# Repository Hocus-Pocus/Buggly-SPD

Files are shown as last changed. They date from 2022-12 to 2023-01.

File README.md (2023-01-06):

# Buggly-SPD
Programmable engine management for the air cooled VW Dual Port 1600 with Mexican EFI OEM parts. The board is a stripped down, "no frills" variant of the official Speeduino V4.4 board with one particular application in mind. A stock, or relatively stock, air cooled VW dual port 1600 engine being converted to EFI using most of the OEM hardware from the Mexican 1600i, and a 36-1 trigger wheel with a VR CKP sensor. It is designed to use waste spark ignition and injectors paired 1&3, 2&4, fired 2 times alternating over the 720 degree engine cycle. The injector pulse is scheduled to be finished when the intake valve reaches the end of its effective duration. With a firing order of 1-4-3-2, half the fuel is injected on an open intake valve, and the other half is injected on a closed intake valve. This should result in a smoother running engine at all speeds and loads as each cylinder gets the same balanced charge mix. This board connects to the Arduino Mega 2560 and is housed in a Hammond enclosure. It has a power supply for the Mega and does all the low voltage processing. It connects to the Buggly Aux board, also in a Hammond enclosuer that has the high current outputs, fuses, relays and terminal strips for connection to vehicle wiring. Header for a Blutooth module added 1-06-23.

  WORK IN PROGRESS

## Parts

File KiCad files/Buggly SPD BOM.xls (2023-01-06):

Buggly SPD BOM
Assignment | Qty | Description | Mfgr | Mfgr # | Digikey #
C17,19,21 | 3 | 10,000pf | Kemet | C315C103K5R5TA | 399-4148-ND
C7,8 | 2 | 47pf | Kemet | C315C470J5G5TA | 399-9737-ND
C5,6,13,14,15,16 | 6 | 0.22uf | Kemet | C320C224K5R5TA | 399-4288-ND
C26 | 1 | 47uf | Panasonic | EEU-FC1H470B | P19658CT-ND
C18,20 | 2 | 1uf | TDK | FK14X7R1E105K | 445-5315-ND
C22 | 1 | 22uf | TDK | FA22X7R1E226MRU06 | 445-180603-1-ND
C1,2,3,4,9,10,11,12,24,25 | 10 | 0.1uf | TDK | FA18X8R1E104KNU06 | 445-180563-1-ND
C23 | 1 | 10uf | Panasonic | EEU-FC1H100LB | P19649CT-ND
D17 | 1 | Diode | Micro | 1N5818-TP | iN5818-TPCT-ND
IC1 | 1 | TVS Array | Little Fuse | SP721APP | F2720-ND
Arduino pins (36) | 1 | Header pins | Amp | 75160-105-36LF | 609-6393-ND
F1 | 1 | Reset Fuse | Bourns | MF-R050 | MF-R050-ND
J15 | 1 | DB25 | Wurth | 618025231221 | 732-618025231221-ND
U1 | 1 | MAP Sensor | NXP | MPXH6115AC6U | MPXH6115AC6U-ND
U1 header pins | 1 | 90 degree | Molex | 0022122041 | 23-0022122041-ND
U3,4,5,6 | 4 | Gate Driver | IXYS | IXDN604PI | CLA335-ND
Sockets for VR Cond, U1,2 | 4 | 4 pos Pin Sockets | 3M | 929850-01-04-10 | 929850-01-04-10
U6 | 1 | Solenoid Driver | STM | ULN2001A | 497-2340-5-ND
U6 socket | 1 | 16 DIP | MillMax | 110-13-316-41-001000 | ED56163-ND
IC1,J16,U3,4,5,6 sockets | 6 | 8 DIP | CNC Tech | 210-1-08-003 | 1175-1467-ND
U7 | 1 | 5V reg | Texas Inst | LM2940T-5.0 | LM2940T-5.0-ND
R3,4,9,10,11,12 | 10 | 470R | Yageo | CFR-25-JB-52-470R | 470QBK-ND
R18 | 1 | 4.7K | Yageo | CFR-25-JB-52-4K7 | 4.7KQBK-ND
R17 | 1 | 24K | Yageo | CFR-25-JB-52-24K | 24KQBK-ND
R19,27,30,31,32,33,34 | 7 | 1K | Yageo | CFR-25-JB-52-1K | 1.0KQBK-ND
R7,8 | 2 | 2.49K | Yageo | 25-FBF-52-2K29 | 2.49KXBK-ND
R13,14,15,35 | 4 | 22R | Stackpole | CF14JT22R0 | CF14JT22R0CT-ND
R16,24,25,26,28,29 | 6 | 100R | Yageo | CFR-25-JB-52-100R | 100QBK-ND
R1 | 1 | 1K 1% | Stackpole | RNMF14FTD1K00 | RNF14FTD1K00CT-ND
R2 | 1 | 3.9K 1% | Stackpole | RNMF14TCK390 | S3.9KCACT-ND
R5,6 | 2 | 51K | Stackpole | CF14JT51K0 | CF14JT51KOCT-ND
RV1 | 1 | Varistor | Panasonic | ERZ-V14D220 | P7307-ND
Q1 | 1 | PNP transistor | Micro | 2N3906-AP | 2N39006-APCT-ND

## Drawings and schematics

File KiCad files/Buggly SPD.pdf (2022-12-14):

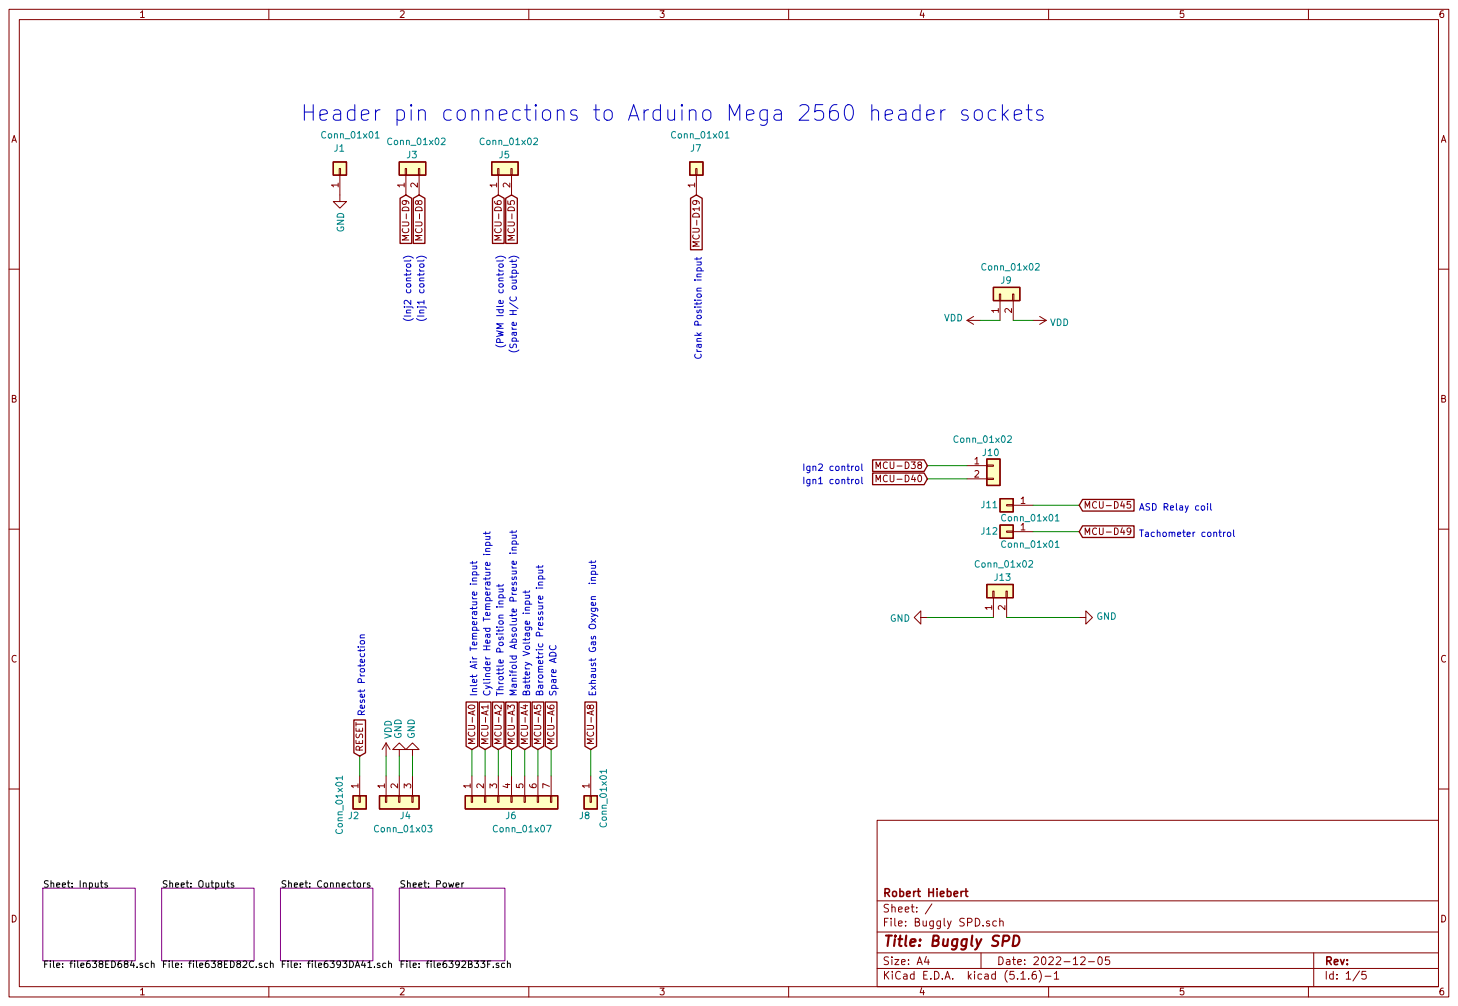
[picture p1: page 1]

Header pin connections to Arduino Mega 2560 header sockets Crank Position input

Ign2 control Spare ADC (Spare H/C output)

ASD Relay coil Tachometer control Reset Protection

Id: 1/5 Title: Buggly SPD

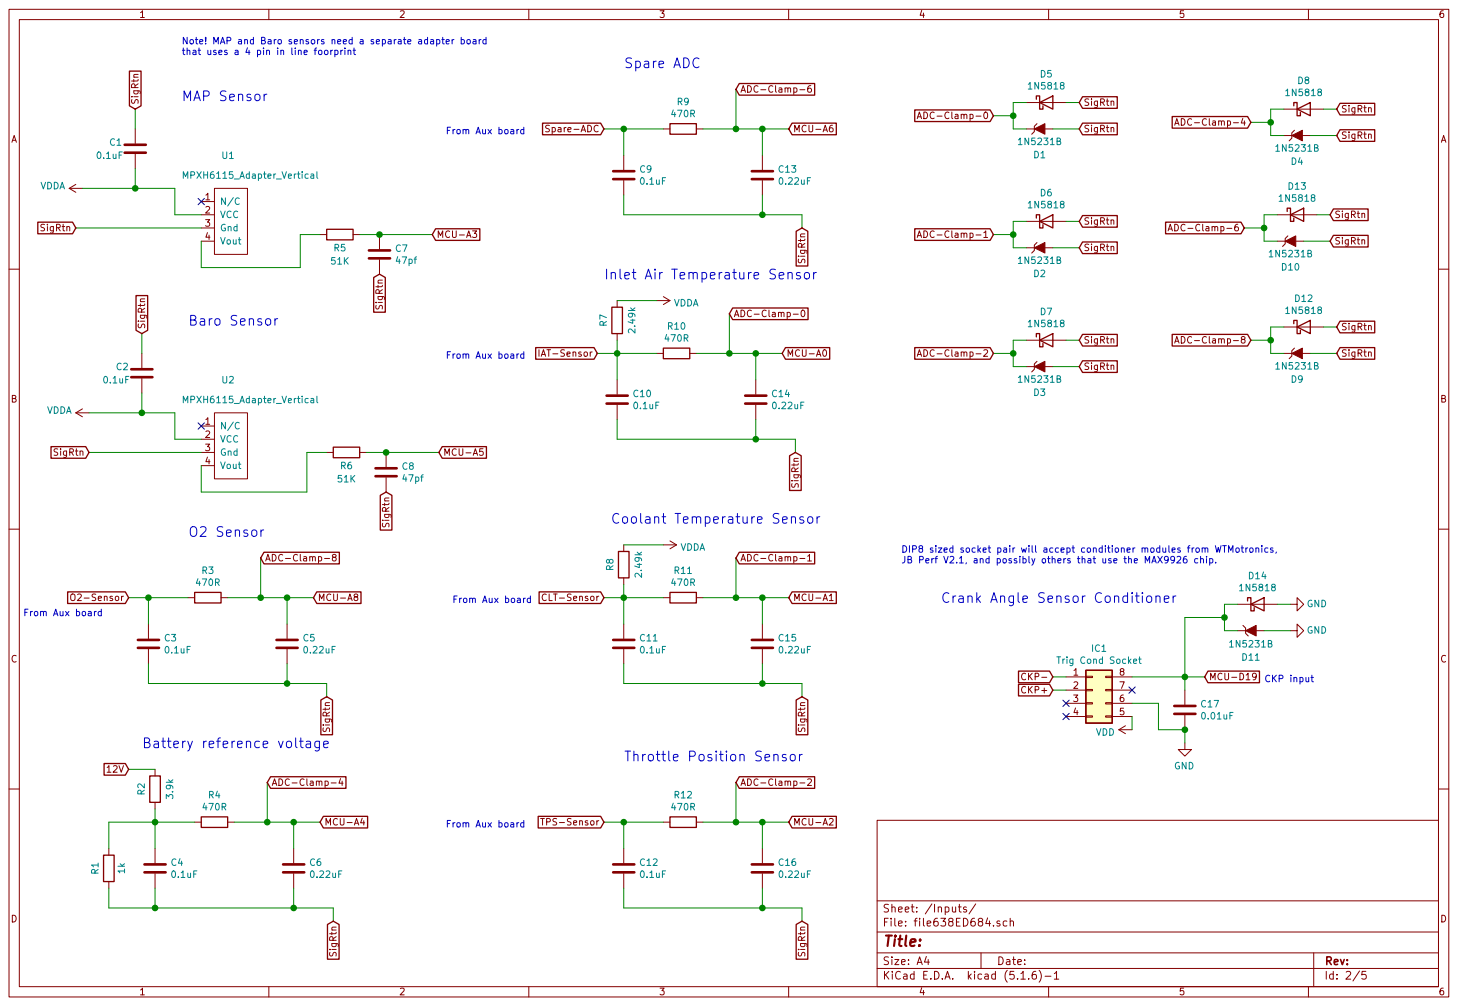
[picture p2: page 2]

Note! MAP and Baro sensors need a separate adapter board
that uses a 4 pin in line foorprint

From Aux board MAP Sensor

IAT-Sensor MCU-A5 MCU-A3 SigRtn

DIP8 sized socket pair will accept conditioner modules from WTMotronics,
JB Perf V2.1, and possibly others that use the MAX9926 chip.

Crank Angle Sensor Conditioner

Id: 2/5 Title: File: file638ED684.sch Sheet: /Inputs/

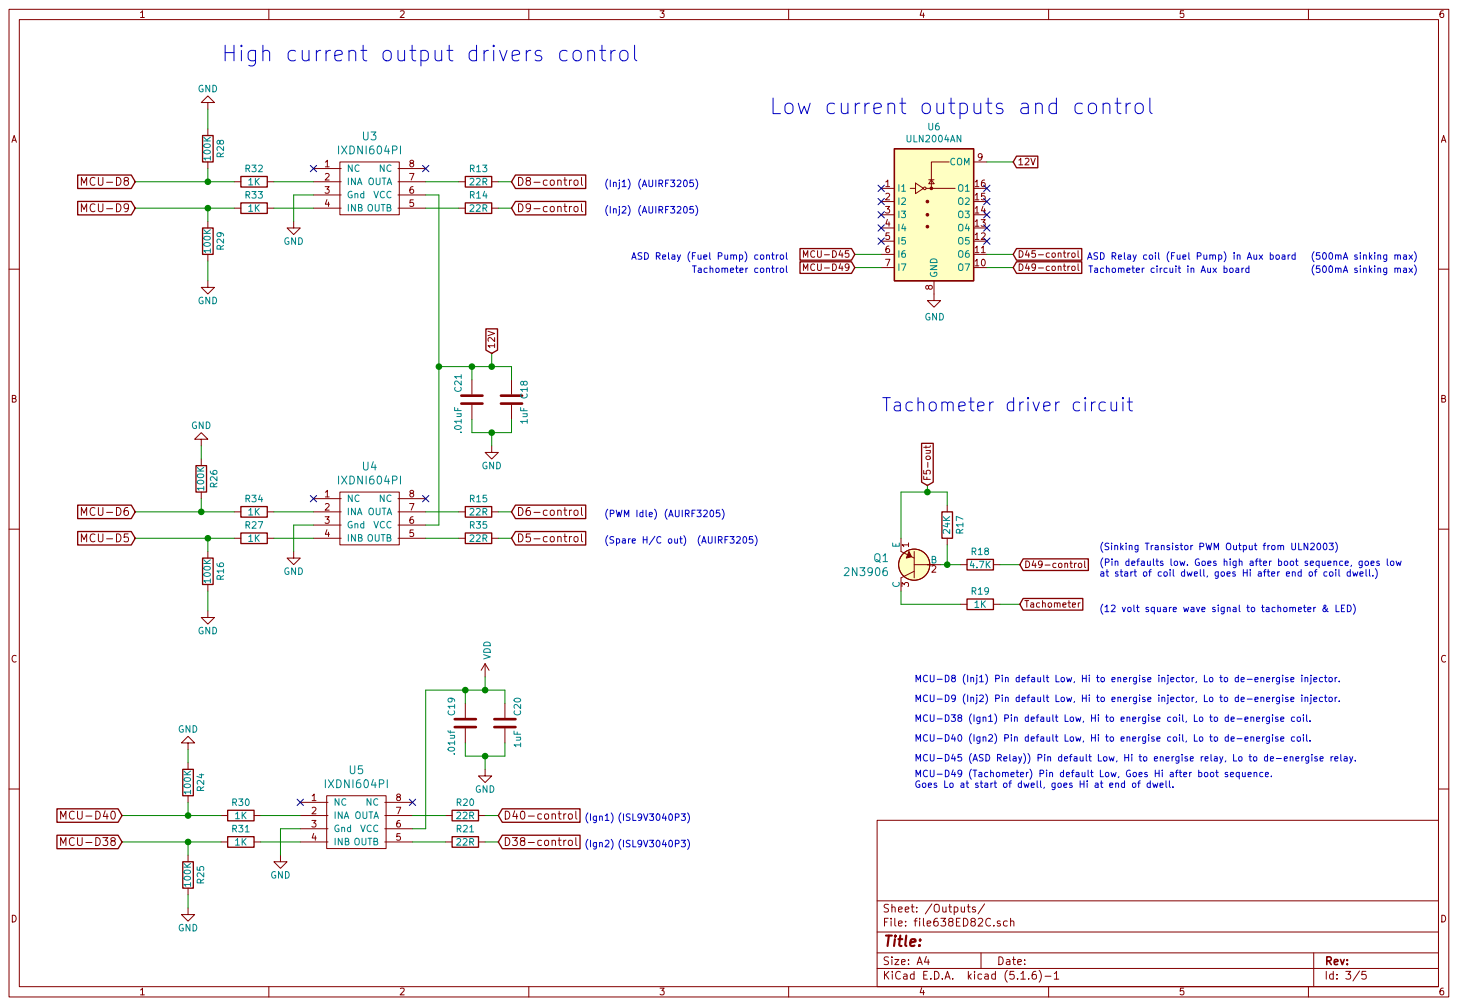
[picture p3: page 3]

Low current outputs and control

8 COM 9 U6 ULN2004AN GND 100K R25 C18 1uF GND GNDGND GND GND

ASD Relay coil (Fuel Pump) in Aux board

(Sinking Transistor PWM Output from ULN2003)
(Pin defaults low. Goes high after boot sequence, goes low
at start of coil dwell, goes Hi after end of coil dwell.)

(12 volt square wave signal to tachometer & LED)

MCU-D8 (Inj1) Pin default Low, Hi to energise injector, Lo to de-energise injector.
MCU-D9 (Inj2) Pin default Low, Hi to energise injector, Lo to de-energise injector.
MCU-D38 (Ign1) Pin default Low, Hi to energise coil, Lo to de-energise coil.
MCU-D40 (Ign2) Pin default Low, Hi to energise coil, Lo to de-energise coil.
MCU-D45 (ASD Relay)) Pin default Low, Hi to energise relay, Lo to de-energise relay.
MCU-D49 (Tachometer) Pin default Low, Goes Hi after boot sequence.
Goes Lo at start of dwell, goes Hi at end of dwell.

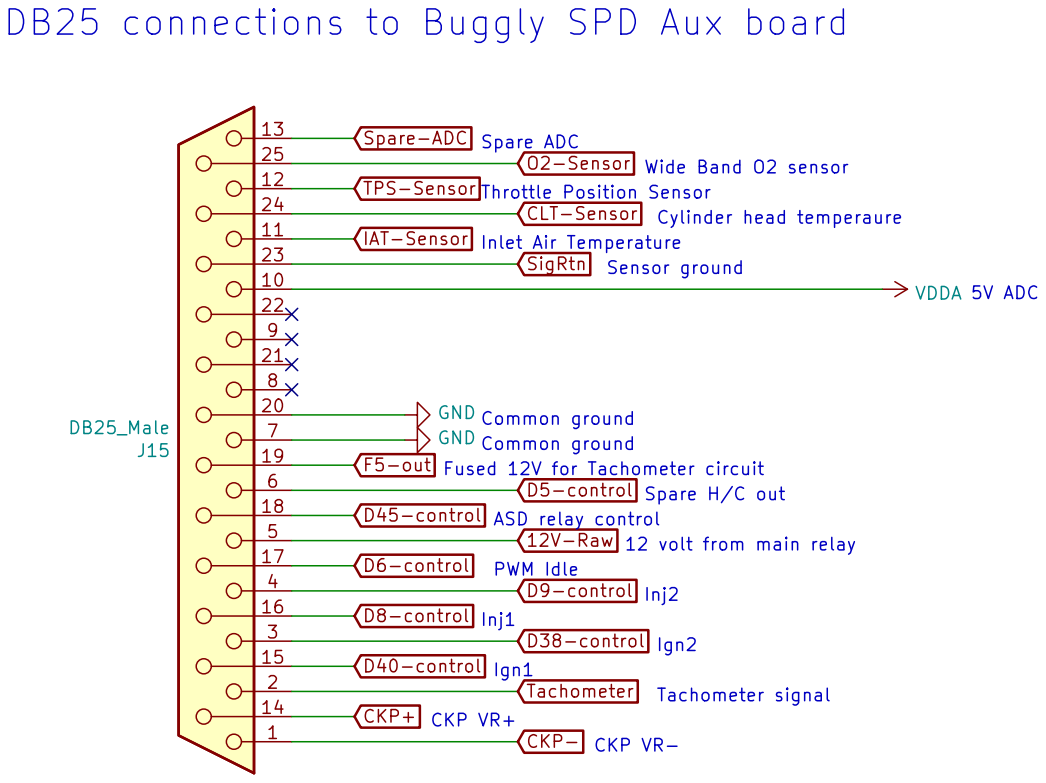
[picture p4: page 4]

5V ADC DB25 connections to Buggly SPD Aux board

Spare H/C out Fused 12V for Tachometer circuit CKP VR+ Spare ADC
Cylinder head temperaure Wide Band O2 sensor Throttle Position Sensor Sensor ground

Id: 4/5 Title: File: file6393DA41.sch Sheet: /Connectors/ GND
Common groundCKP VR-
Common ground

ASD relay control PWM Idle
12V-Raw

12 volt from main relay

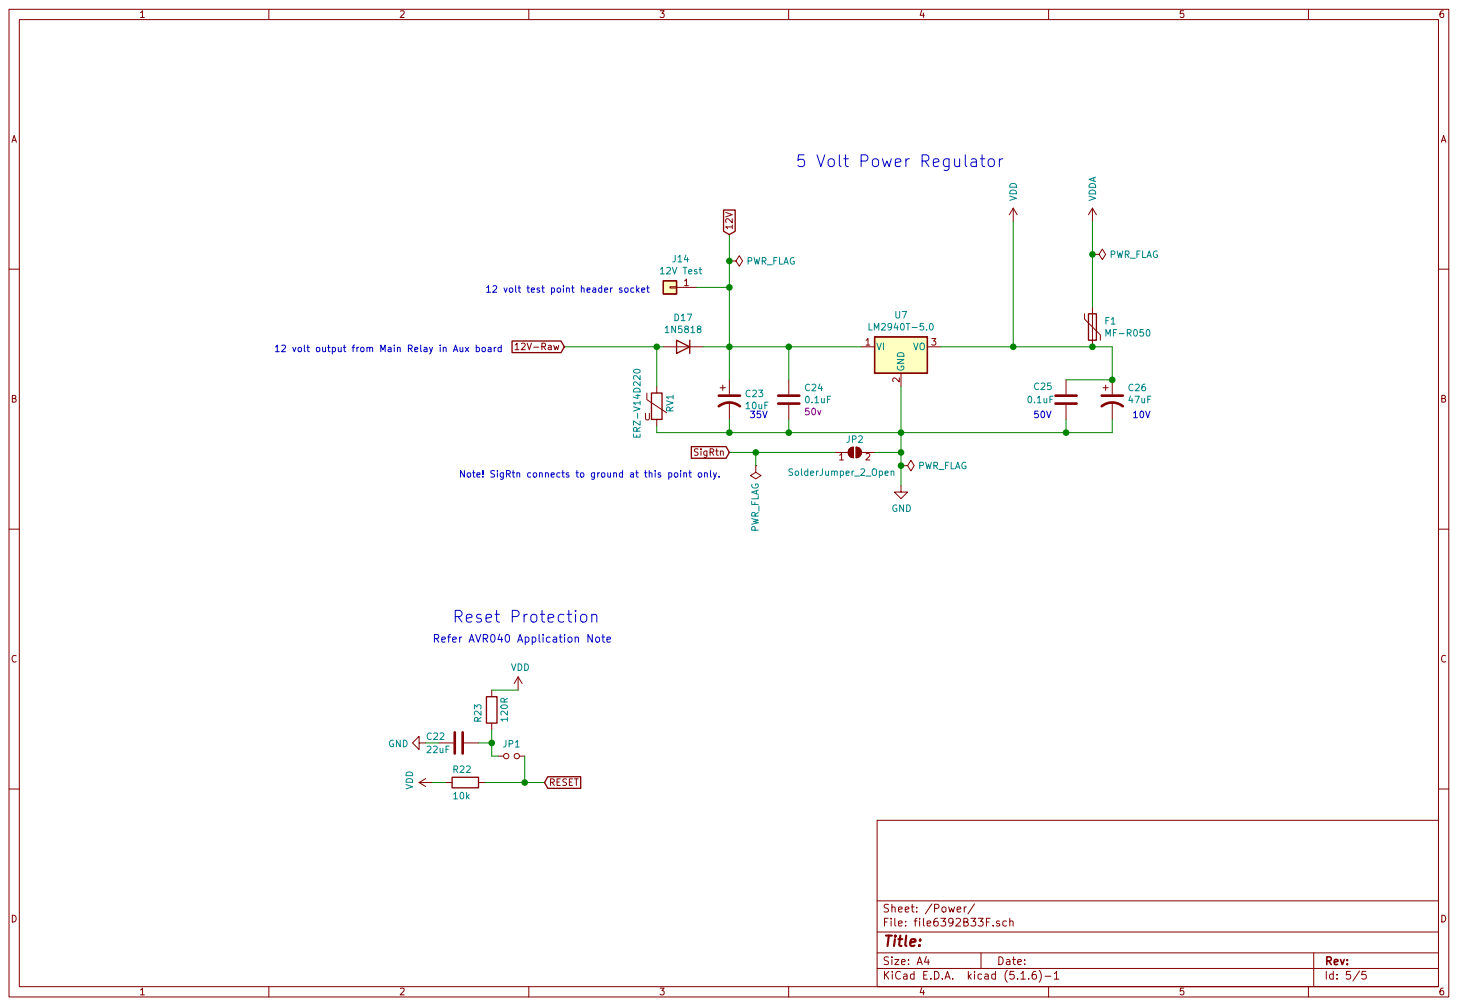
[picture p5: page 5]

12 volt test point header socket

12 volt output from Main Relay in Aux board

Note! SigRtn connects to ground at this point only.

Id: 5/5 Title: File: file6392B33F.sch Sheet: /Power/

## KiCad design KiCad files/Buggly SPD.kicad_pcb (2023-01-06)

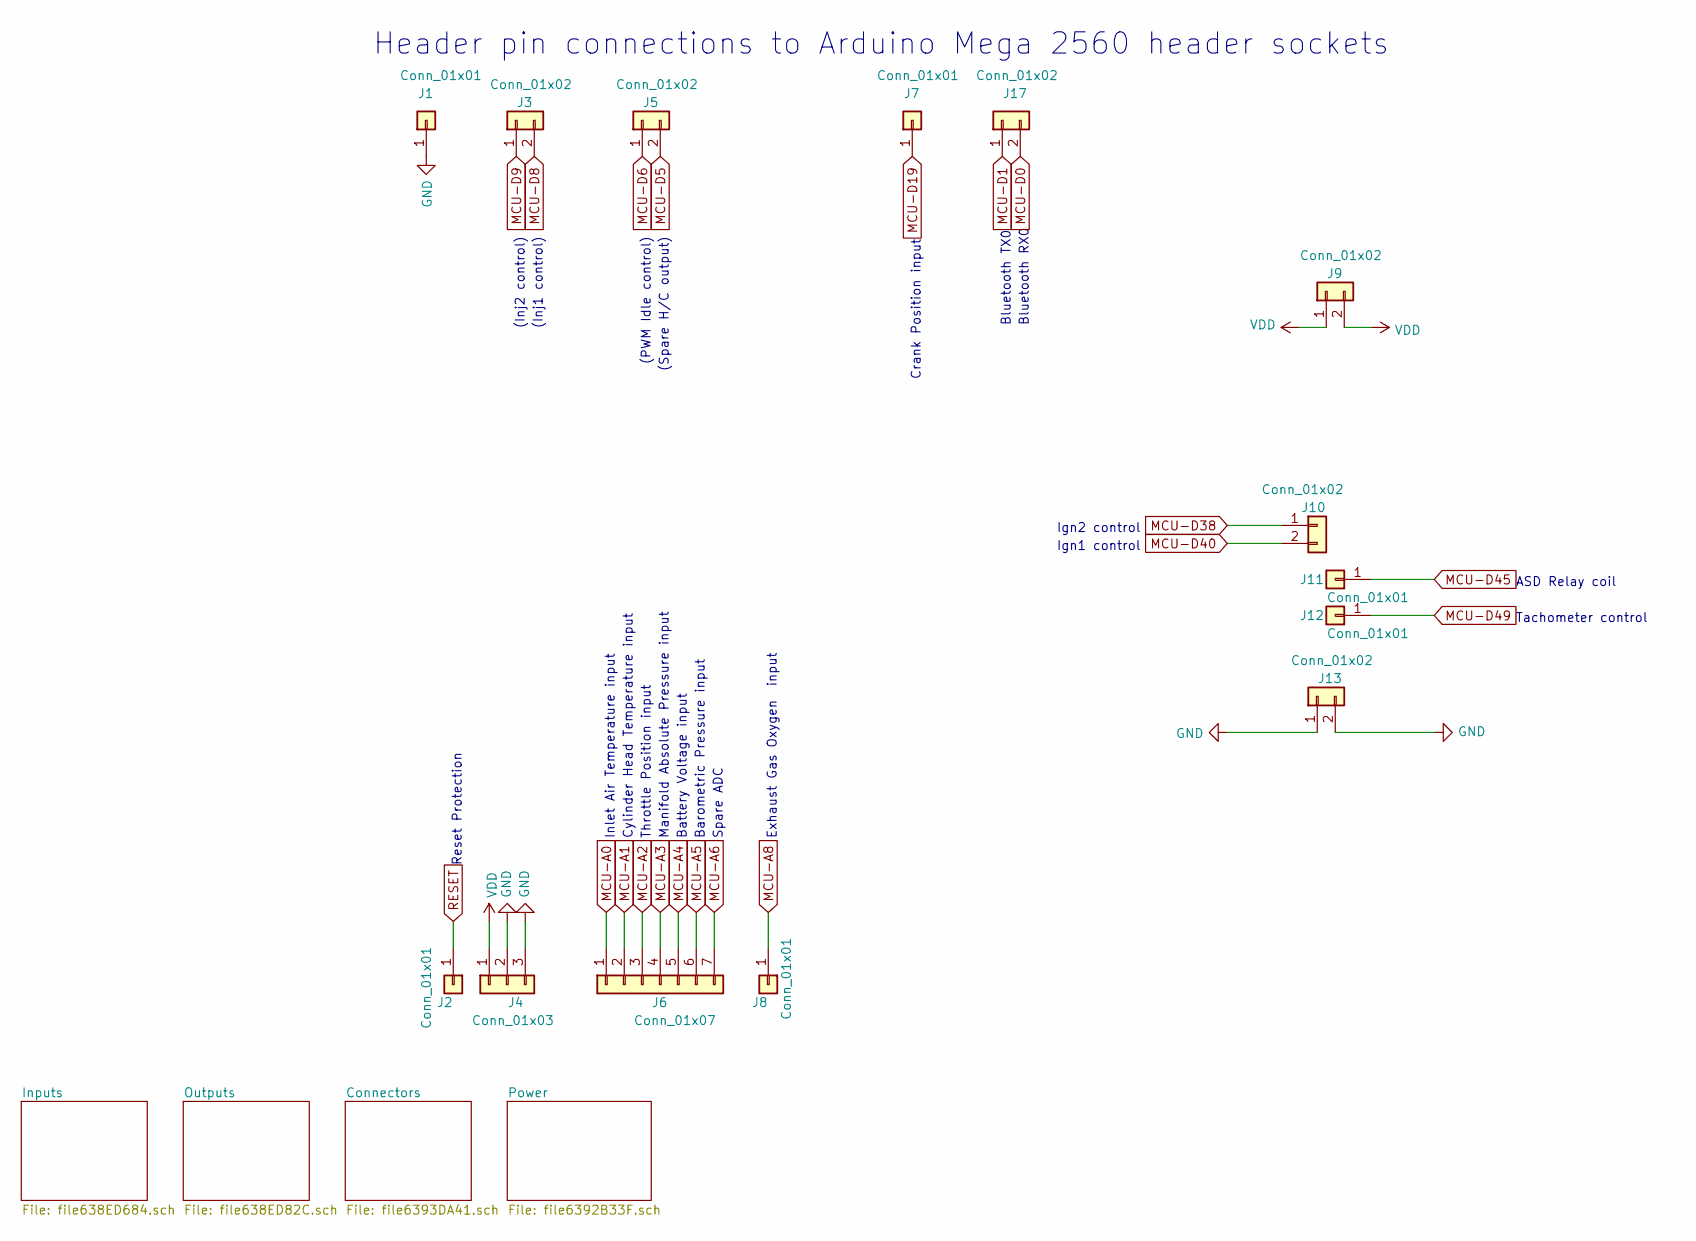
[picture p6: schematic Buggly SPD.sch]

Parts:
J1, J2, J7, J8, J11, J12: Conn_01x01; PinHeader_1x01_P2.54mm_Vertical
J3, J5, J9, J10, J13, J17: Conn_01x02; PinHeader_1x02_P2.54mm_Vertical
J4: Conn_01x03; PinHeader_1x03_P2.54mm_Vertical
J6: Conn_01x07; PinHeader_1x07_P2.54mm_Vertical

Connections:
ADC-Clamp-0: J6.1; also elsewhere on the board
ADC-Clamp-1: J6.2; also elsewhere on the board
ADC-Clamp-2: J6.3; also elsewhere on the board
ADC-Clamp-4: J6.5; also elsewhere on the board
ADC-Clamp-6: J6.7; also elsewhere on the board
ADC-Clamp-8: J8.1; also elsewhere on the board
GND: J1.1, J4.2, J4.3, J13.1, J13.2; also elsewhere on the board
MCU-A3: J6.4; also elsewhere on the board
MCU-A5: J6.6; also elsewhere on the board
MCU-D0: J17.2; also elsewhere on the board
MCU-D1: J17.1; also elsewhere on the board
MCU-D5: J5.2; also elsewhere on the board
MCU-D6: J5.1; also elsewhere on the board
MCU-D8: J3.2; also elsewhere on the board
MCU-D9: J3.1; also elsewhere on the board
MCU-D19: J7.1; also elsewhere on the board
MCU-D38: J10.1; also elsewhere on the board
MCU-D40: J10.2; also elsewhere on the board
MCU-D45: J11.1; also elsewhere on the board
MCU-D49: J12.1; also elsewhere on the board
RESET: J2.1; also elsewhere on the board
VDD: J4.1, J9.1, J9.2; also elsewhere on the board

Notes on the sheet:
Ign1 control
ASD Relay coil
Ign2 control
Tachometer control
Reset Protection
Inlet Air Temperature input
Cylinder Head Temperature input
Throttle Position input
Exhaust Gas Oxygen input
Battery Voltage input
Manifold Absolute Pressure input
Barometric Pressure input
(Inj1 control)
(PWM Idle control)
(Inj2 control)
Header pin connections to Arduino Mega 2560 header sockets
Crank Position input
(Spare H/C output)
Spare ADC
Bluetooth RX0
Bluetooth TX0

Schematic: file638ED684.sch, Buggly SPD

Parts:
C1, C2: 0.1uF; C_Disc_D5.0mm_W2.5mm_P2.50mm; Manufacturer_Part_Number FA18X7R1H103KNU06; Digikey Part Number 445-174244-1-ND
C3, C4, C9, C10, C11, C12: 0.1uF; C_Disc_D5.0mm_W2.5mm_P2.50mm; Manufacturer_Part_Number FA18X8R1E104KNU06; Digikey Part Number 445-180563-1-ND
C5, C6, C13, C14, C15, C16: 0.22uF; C_Disc_D5.0mm_W2.5mm_P2.50mm; Manufacturer_Part_Number FA18X8R1E224KRU06; Digikey Part Number 445-180564-1-ND
C7, C8: 47pf; C_Disc_D5.0mm_W2.5mm_P2.50mm; Manufacturer_Part_Number FA18NP01H471JNU06; Digikey Part Number 445-180522-1-ND
C17: 0.01uF; C_Disc_D5.0mm_W2.5mm_P2.50mm; Manufacturer_Part_Number FA18X7R1H103KNU06; Digikey Part Number 445-174244-1-ND
IC1: Trig Cond Socket; DIP-8_W7.62mm_Socket
J16: SP721APP; DIP-8_W7.62mm
J18: Conn_01x04; PinSocket_1x04_P2.54mm_Horizontal
R1: 1k; R_Axial_DIN0207_L6.3mm_D2.5mm_P7.62mm_Horizontal; Manufacturer_Part_Number MBA02040C1001FRP00; Digikey Part Number BC1.00KXCT-ND
R2: 3.9k; R_Axial_DIN0207_L6.3mm_D2.5mm_P7.62mm_Horizontal; Manufacturer_Part_Number MBA02040C3901FCT00; Digikey Part Number BC3272CT-ND
R3, R4, R9, R10, R11, R12: 470R; R_Axial_DIN0207_L6.3mm_D2.5mm_P7.62mm_Horizontal; Manufacturer_Part_Number MBA02040C4700FRP00; Digikey Part Number BC3516CT-ND
R5, R6: 51K; R_Axial_DIN0207_L6.3mm_D2.5mm_P7.62mm_Horizontal; Manufacturer_Part_Number MBA02040C4700FRP00; Digikey Part Number BC3516CT-ND
R7, R8: 2.49k; R_Axial_DIN0207_L6.3mm_D2.5mm_P7.62mm_Horizontal; Manufacturer_Part_Number MBA02040C2491FRP00; Digikey Part Number BC2.49KXCT-ND
R36: 1K; R_Axial_DIN0207_L6.3mm_D2.5mm_P7.62mm_Horizontal; Manufacturer_Part_Number MBA02040C4700FRP00; Digikey Part Number BC3516CT-ND
R37: 2.2K; R_Axial_DIN0207_L6.3mm_D2.5mm_P7.62mm_Horizontal; Manufacturer_Part_Number MBA02040C4700FRP00; Digikey Part Number BC3516CT-ND
U1, U2: MPXH6115_Adapter_Vertical

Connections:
12V: R2.2; also elsewhere on the board
ADC-Clamp-0: C14.1, J16.1, R10.1; also elsewhere on the board
ADC-Clamp-1: C15.1, J16.2, R11.1; also elsewhere on the board
ADC-Clamp-2: C16.1, J16.3, R12.1; also elsewhere on the board
ADC-Clamp-4: C6.1, J16.5, R4.1; also elsewhere on the board
ADC-Clamp-6: C13.1, J16.6, R9.1; also elsewhere on the board
ADC-Clamp-8: C5.1, J16.7, R3.1; also elsewhere on the board
CKP+: IC1.2; also elsewhere on the board
CKP-: IC1.1; also elsewhere on the board
CLT-Sensor: C11.1, R8.1, R11.2; also elsewhere on the board
GND: C17.2, IC1.6, J18.2, R37.1; also elsewhere on the board
IAT-Sensor: C10.1, R7.1, R10.2; also elsewhere on the board
MCU-A3: C7.1, R5.1; also elsewhere on the board
MCU-A5: C8.1, R6.1; also elsewhere on the board
MCU-D0: J18.3; also elsewhere on the board
MCU-D1: R36.2; also elsewhere on the board
MCU-D19: C17.1, IC1.8; also elsewhere on the board
unnamed: C4.1, R1.2, R2.1, R4.2
unnamed: J18.4, R36.1, R37.2
unnamed: R5.2, U1.4
unnamed: R6.2, U2.4
O2-Sensor: C3.1, R3.2; also elsewhere on the board
SigRtn: C1.1, C2.1, C3.2, C4.2, C5.2, C6.2, C7.2, C8.2, C9.2, C10.2, C11.2, C12.2, C13.2, C14.2, C15.2, C16.2, J16.4, R1.1, U1.3, U2.3; also elsewhere on the board
Spare-ADC: C9.1, R9.2; also elsewhere on the board
TPS-Sensor: C12.1, R12.2; also elsewhere on the board
VDD: IC1.5, J18.1; also elsewhere on the board
VDDA: C1.2, C2.2, J16.8, R7.2, R8.2, U1.2, U2.2; also elsewhere on the board

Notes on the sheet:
MAP Sensor
O2 Sensor
Throttle Position Sensor
Inlet Air Temperature Sensor
Coolant Temperature Sensor
Battery reference voltage
Baro Sensor
From Aux board
Note! MAP and Baro sensors need a separate adapter board that uses a 4 pin in line foorprint
CKP input
DIP8 sized socket pair will accept conditioner modules from WTMotronics, JB Perf V2.1, and possibly others that use the MAX9926 chip.
Crank Angle Sensor Conditioner
Spare ADC
IAT
CLT
TPS
BAT
Spare
ADC Clamps
DSD Tech HC-06 Bluetooth module header
Gnd
BT TX
BT RX
RX0
TX0

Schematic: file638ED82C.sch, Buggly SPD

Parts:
C18, C20: 1uF; C_Disc_D5.0mm_W2.5mm_P2.50mm
C19: .01uf; C_Disc_D5.0mm_W2.5mm_P2.50mm
C21: .01uF; C_Disc_D5.0mm_W2.5mm_P2.50mm
Q1: 2N3906; TO-92_Inline_Wide; MPN 2N3906; Digi-Key_PN 2N3906CS-ND
R13, R14, R15, R20, R21, R35: 22R; R_Axial_DIN0207_L6.3mm_D2.5mm_P7.62mm_Horizontal
R16, R24, R25, R26, R28, R29: 100K; R_Axial_DIN0207_L6.3mm_D2.5mm_P7.62mm_Horizontal
R17: 24K; R_Axial_DIN0207_L6.3mm_D2.5mm_P7.62mm_Horizontal
R18: 4.7K; R_Axial_DIN0207_L6.3mm_D2.5mm_P7.62mm_Horizontal
R19, R27, R30, R31, R32, R33, R34: 1K; R_Axial_DIN0207_L6.3mm_D2.5mm_P7.62mm_Horizontal
U3, U4, U5: IXDNI604PI; DIP-8_W7.62mm
U6: ULN2004AN; DIP-16_W7.62mm; Manufacturer_Part_Number ULN2003AIN‎; Digikey Part Number 296-16971-5-ND

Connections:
12V: C18.2, C21.2, U3.6, U4.6, U6.9 (COM); also elsewhere on the board
D5-control: R35.1; also elsewhere on the board
D6-control: R15.1; also elsewhere on the board
D8-control: R13.1; also elsewhere on the board
D9-control: R14.1; also elsewhere on the board
D38-control: R21.1; also elsewhere on the board
D40-control: R20.1; also elsewhere on the board
D45-control: U6.11 (O6); also elsewhere on the board
D49-control: R18.1, U6.10 (O7)
F5-out: Q1.1 (E), R17.2; also elsewhere on the board
GND: C18.1, C19.1, C20.1, C21.1, R16.1, R24.2, R25.1, R26.2, R28.2, R29.1, U3.3, U4.3, U5.3, U6.8 (GND); also elsewhere on the board
MCU-D5: R16.2, R27.2; also elsewhere on the board
MCU-D6: R26.1, R34.2; also elsewhere on the board
MCU-D8: R28.1, R32.2; also elsewhere on the board
MCU-D9: R29.2, R33.2; also elsewhere on the board
MCU-D38: R25.2, R31.2; also elsewhere on the board
MCU-D40: R24.1, R30.2; also elsewhere on the board
MCU-D45: U6.6 (I6); also elsewhere on the board
MCU-D49: U6.7 (I7); also elsewhere on the board
unnamed: Q1.2 (B), R17.1, R18.2
unnamed: Q1.3 (C), R19.2
unnamed: R13.2, U3.7
unnamed: R14.2, U3.5
unnamed: R15.2, U4.7
unnamed: R20.2, U5.7
unnamed: R21.2, U5.5
unnamed: R27.1, U4.4
unnamed: R30.1, U5.2
unnamed: R31.1, U5.4
unnamed: R32.1, U3.2
unnamed: R33.1, U3.4
unnamed: R34.1, U4.2
unnamed: R35.2, U4.5
Tachometer: R19.1; also elsewhere on the board
VDD: C19.2, C20.2, U5.6; also elsewhere on the board

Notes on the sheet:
(Inj1)
(Inj2)
(PWM Idle)
ASD Relay coil (Fuel Pump) in Aux board
Tachometer circuit in Aux board
Tachometer control
ASD Relay (Fuel Pump) control
(Ign2)
(Ign1)
(500mA sinking max)
High current output drivers control
Low current outputs and control
MCU-D8 (Inj1) Pin default Low, Hi to energise injector, Lo to de-energise injector.
MCU-D9 (Inj2) Pin default Low, Hi to energise injector, Lo to de-energise injector.
MCU-D38 (Ign1) Pin default Low, Hi to energise coil, Lo to de-energise coil.
MCU-D40 (Ign2) Pin default Low, Hi to energise coil, Lo to de-energise coil.
MCU-D45 (ASD Relay)) Pin default Low, Hi to energise relay, Lo to de-energise relay.
MCU-D49 (Tachometer) Pin default Low, Goes Hi after boot sequence. Goes Lo at start of dwell, goes Hi at end of dwell.
(Sinking Transistor PWM Output from ULN2003)
(12 volt square wave signal to tachometer & LED)
Tachometer driver circuit
(Pin defaults low. Goes high after boot sequence, goes low at start of coil dwell, goes Hi after end of coil dwell.)
(AUIRF3205)
(ISL9V3040P3)
(Spare H/C out)

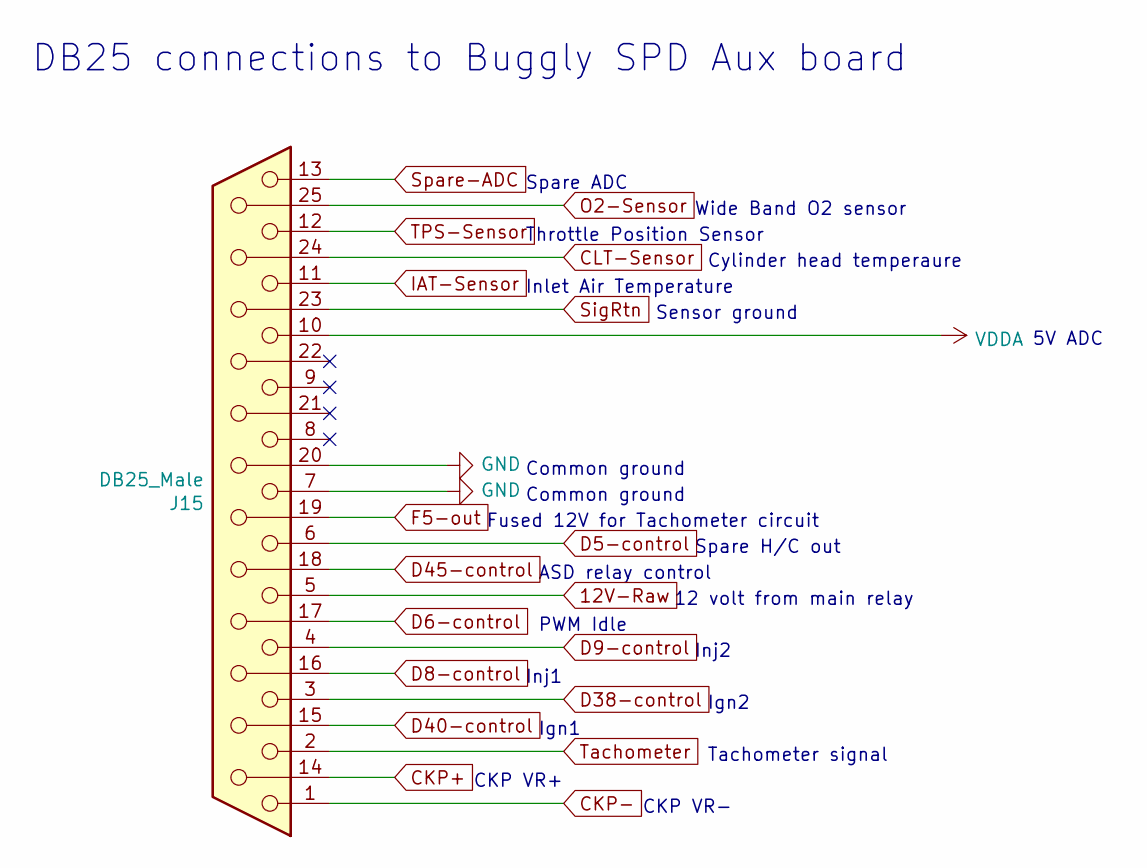
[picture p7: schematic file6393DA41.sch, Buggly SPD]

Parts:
J15: DB25_Male; DSUB-25_Male_Horizontal_P2.77x2.84mm_EdgePinOffset4.94mm_Ho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

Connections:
12V-Raw: J15.5; also elsewhere on the board
CKP+: J15.14; also elsewhere on the board
CKP-: J15.1; also elsewhere on the board
CLT-Sensor: J15.24; also elsewhere on the board
D5-control: J15.6; also elsewhere on the board
D6-control: J15.17; also elsewhere on the board
D8-control: J15.16; also elsewhere on the board
D9-control: J15.4; also elsewhere on the board
D38-control: J15.3; also elsewhere on the board
D40-control: J15.15; also elsewhere on the board
D45-control: J15.18; also elsewhere on the board
F5-out: J15.19; also elsewhere on the board
GND: J15.7, J15.20; also elsewhere on the board
IAT-Sensor: J15.11; also elsewhere on the board
O2-Sensor: J15.25; also elsewhere on the board
SigRtn: J15.23; also elsewhere on the board
Spare-ADC: J15.13; also elsewhere on the board
TPS-Sensor: J15.12; also elsewhere on the board
Tachometer: J15.2; also elsewhere on the board
VDDA: J15.10; also elsewhere on the board

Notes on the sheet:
Fused 12V for Tachometer circuit
CKP VR+
5V ADC
Inlet Air Temperature
Cylinder head temperaure
Wide Band O2 sensor
Throttle Position Sensor
Sensor ground
Common ground
CKP VR-
Ign1
ASD relay control
PWM Idle
Inj1
12 volt from main relay
DB25 connections to Buggly SPD Aux board
Spare ADC
Inj2
Tachometer signal
Ign2
Spare H/C out

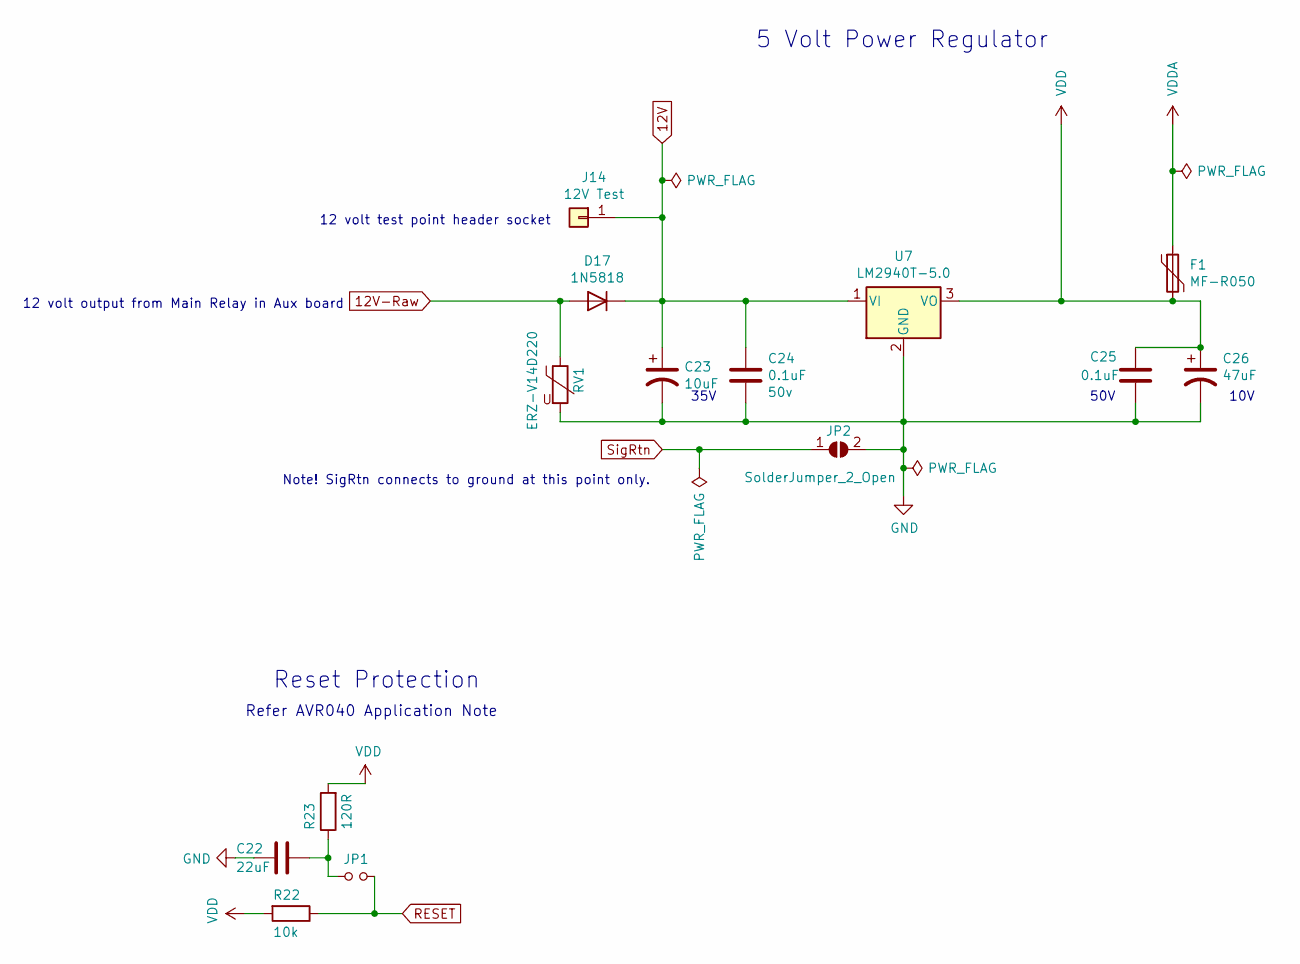
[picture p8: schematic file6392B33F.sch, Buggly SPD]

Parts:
C22: 22uF; C_Disc_D7.5mm_W5.0mm_P5.00mm; Manufacturer_Part_Number FA22X7R1E226MRU06; Digikey Part Number 445-180603-1-ND
C23: 10uF; CP_Radial_D5.0mm_P2.00mm; Voltage 50v; Manufacturer_Part_Number EEU-FC1H100L; Digikey Part Number P10316-ND
C24: 0.1uF; C_Disc_D5.0mm_W2.5mm_P2.50mm; Voltage 50v; Manufacturer_Part_Number FA18X8R1E104KNU06; Digikey Part Number 445-180563-1-ND
C25: 0.1uF; C_Disc_D5.0mm_W2.5mm_P2.50mm; Manufacturer_Part_Number FA18X8R1E104KNU06; Digikey Part Number 445-180563-1-ND
C26: 47uF; CP_Radial_D8.0mm_P5.00mm; Manufacturer_Part_Number EEU-FC1H470B; Digikey Part Number P19658CT-ND
D17: 1N5818; D_DO-41_SOD81_P10.16mm_Horizontal
F1: MF-R050; Fuse_BelFuse_0ZRE0100FF_L18.7mm_W5.1mm; Manufacturer_Part_Number 0ZRP0050FF1E; Digikey Part Number 507-2403-ND
J14: 12V Test; PinSocket_1x01_P2.54mm_Vertical
JP1: Jumper_NO_Small; PinHeader_1x02_P2.54mm_Vertical
JP2: SolderJumper_2_Open; SolderJumper-2_P1.3mm_Open_RoundedPad1.0x1.5mm
R22: 10k; R_Axial_DIN0207_L6.3mm_D2.5mm_P7.62mm_Horizontal; Manufacturer_Part_Number MBA02040C1002FRP00; Digikey Part Number BC10.0KXCT-ND
R23: 120R; R_Axial_DIN0207_L6.3mm_D2.5mm_P7.62mm_Horizontal; Manufacturer_Part_Number MBA02040C1200FC100; Digikey Part Number BC3453CT-ND
RV1: ERZ-V14D220; RV_Disc_D15.5mm_W4.7mm_P7.5mm
U7: LM2940T-5.0; TO-220-3_Horizontal_TabDown; Manufacturer_Part_Number NCV7805BTG; Digikey Part Number NCV7805BTGOS-ND

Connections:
12V: C23.1, C24.1, D17.1 (K), J14.1, U7.1 (VI); also elsewhere on the board
12V-Raw: D17.2 (A), RV1.1; also elsewhere on the board
GND: C22.2, C23.2, C24.2, C25.2, C26.2, JP2.2 (B), RV1.2, U7.2 (GND); also elsewhere on the board
unnamed: C22.1, JP1.1, R23.1
RESET: JP1.2, R22.1; also elsewhere on the board
SigRtn: JP2.1 (A); also elsewhere on the board
VDD: C25.1, C26.1, F1.2, R22.2, R23.2, U7.3 (VO); also elsewhere on the board
VDDA: F1.1; also elsewhere on the board

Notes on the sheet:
5 Volt Power Regulator
Reset Protection
Refer AVR040 Application Note
12 volt output from Main Relay in Aux board
10V
50V
35V
12 volt test point header socket
Note! SigRtn connects to ground at this point only.

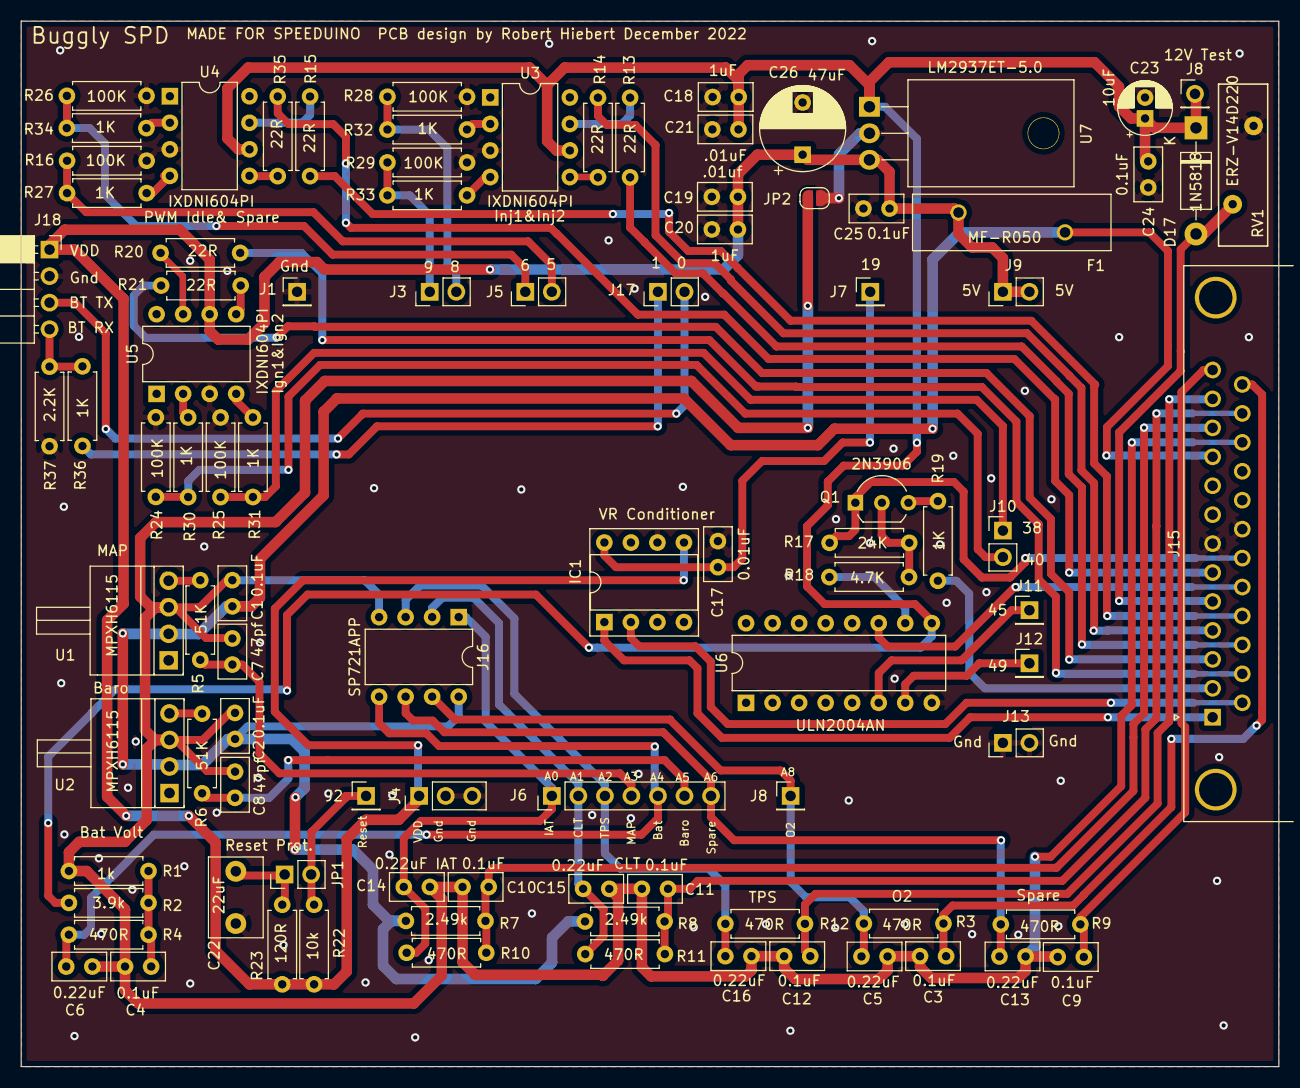
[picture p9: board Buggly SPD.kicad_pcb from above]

Board: 2 copper layers, 120.4 x 100.1 mm, 95 parts (0 on the bottom side), 62 nets.

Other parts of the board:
J8#2: 12V Test; Jumper-Pad

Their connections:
12V: J8#2.1; also elsewhere on the board
